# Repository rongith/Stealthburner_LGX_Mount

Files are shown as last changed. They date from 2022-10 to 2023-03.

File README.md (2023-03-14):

# Stealthburner_LGX_Mount

***

1. [Introduction](#introduction)
2. [Credits](#credits)
3. [Parts](#parts)
4. [LGX Mounting](#lgx-mounting)
5. [Features I took care of](#features-i-took-care-of)

***

## Introduction

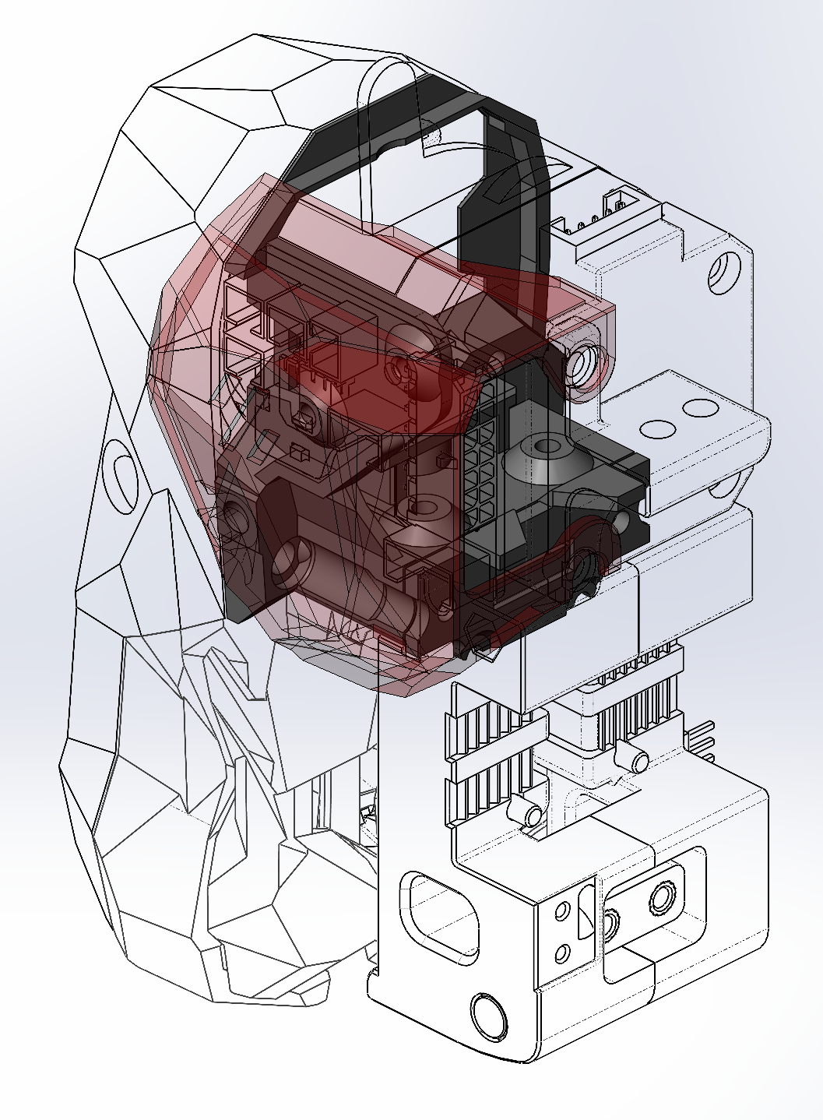
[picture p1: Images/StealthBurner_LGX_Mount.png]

I didn't find a mounting with some bells and whistles I wanted to use my LGX with the Stealthburner. Then I designed my own.

It is be compatible with both versions of rail carriage. The one we screw on the back (Afterburner carriage with CW1) and the one we screw on the front (Stealthburner carriage with CW2).

The Afterburner PCB (LDO) mounting is optionnal. I'm trying to implement the Stealthburner PCB.

The 3D printed parts may not follow the Voron design recommendations.

All photos are not of the same design iteration. I didn't want to shoot the whole sequence of the mounting each time I improved the parts.

## Credits

- Thanx to @errornumber419 for the design of adding the PCB support directly on the mounting.

- The cover is based on wile.e1 cover for Stealthburner and CW1 (<https://github.com/VoronDesign/VoronUsers/tree/master/printer_mods/wile-e1/Stealthburner_CW1_PCB_Cover>)

## Parts

- Mounting options
  - Normal files are in "Standard" folder
  - OctotapV2 files are in "OctotapV2" folder. You can use OctotapV2 files even if you don't have it. It does only level up the mounting to 2mm to set some clearance for the OctotapVé PCB.

| CW1<br>carriage | CW2<br>carriage | All in<br>one part | PCB<br>Support | Files to print|
|:---:|:---:|:---:|:---:|---|
|No|Yes| Yes | No | LGX_SB_Mount-rxxx - 1-2-NoPCB |
|No|Yes| Yes | Yes | LGX_SB_Mount-rxxx - 1-2-PCB |
|Yes|Yes| No | No | LGX_SB_Mount-rxxx - 1-NoPCB / LGX_SB_Mount-rxxx - 2 |
|Yes|Yes| No | Yes | LGX_SB_Mount-rxxx - 1-PCB / LGX_SB_Mount-rxxx - 2|

- Cover

| File to print |
|---|
| [a]_LGX_SB_Cover-rxxx - Standard |

- Additional hardware
  - M3x20 (x2). SHCS / ISO 4762 recommended
  - M3x30 (x2). SHCS / ISO 4762 recommended (M3x25 is enough for the screws on the back mounting)
  - M3x6 (x2). BHCS / ISO7380-1 for the PCB in case you have one.
  - M3 Heat insert (x3).

## LGX Mounting

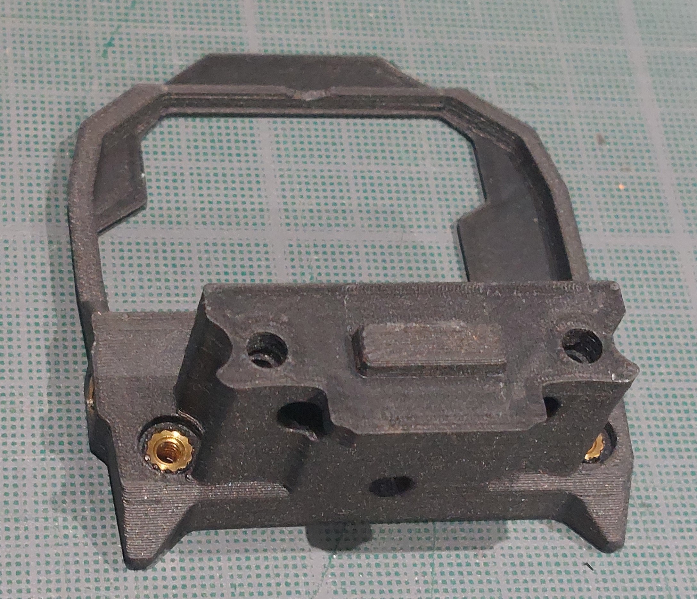
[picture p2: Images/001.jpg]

Put insert in the 3 holes.

Take care to get the insert quite well straight. It is for the Stealthburner to move easily along the M3x25 screws afterward when you want to swap the toolhead.

The insert on the left (of the photo) edge is to screw the cover.

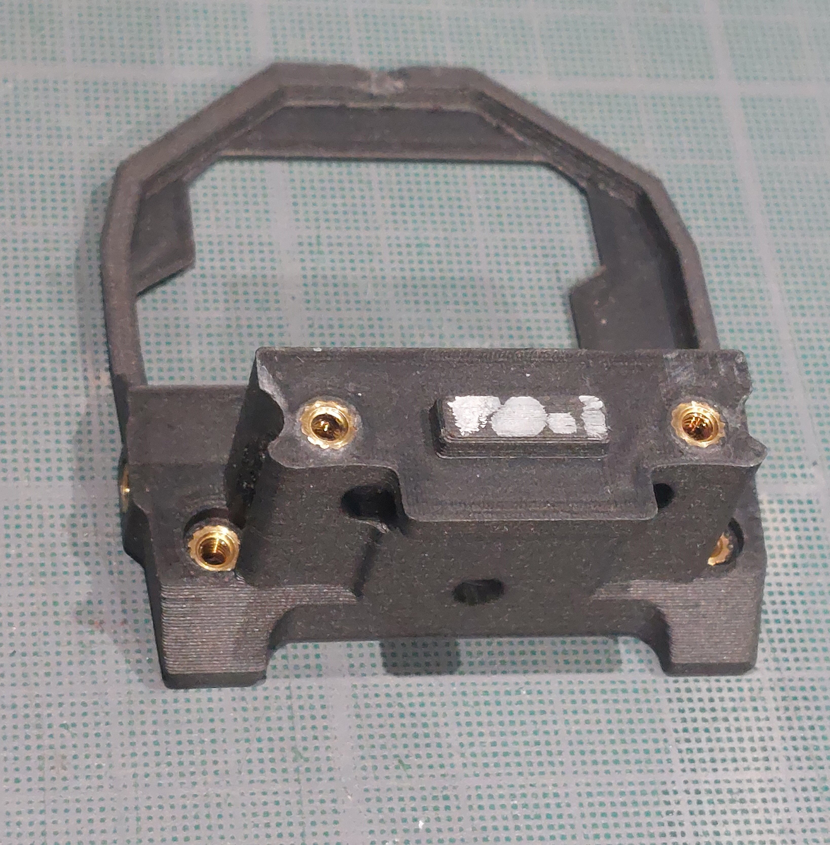
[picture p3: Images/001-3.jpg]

In case you want to use the rail carriage that has holes to screw on the back (CW1), add two more inserts in the back of the part.


    Add the back of the mounting. It should fit on the rectangular joint. Later, it doesn't have to be separated from the mounting. Then I choose to glue it but it is really not mandatory.

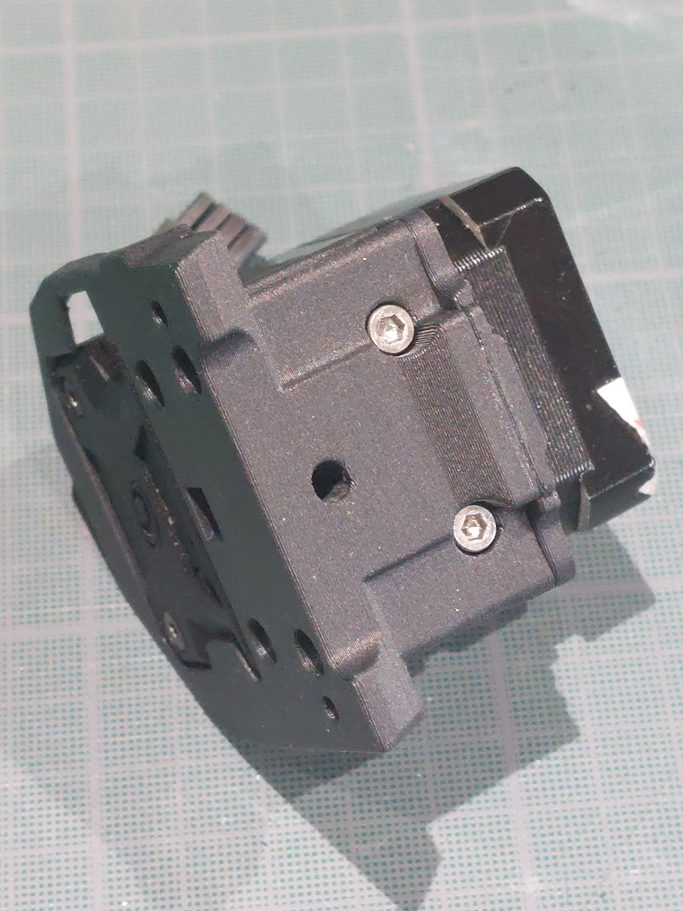
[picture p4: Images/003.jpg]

Screw the bottom with 2 M3x20.

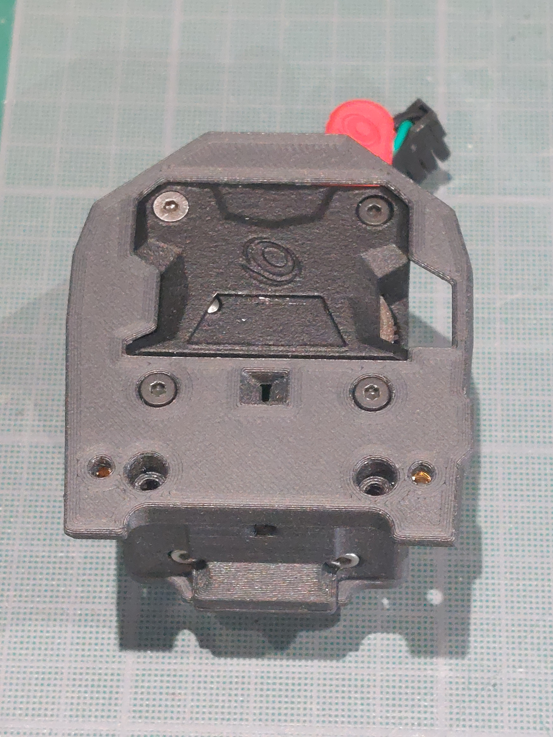
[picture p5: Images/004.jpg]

Screw the front with the provided Bondtech LGX M3x27.

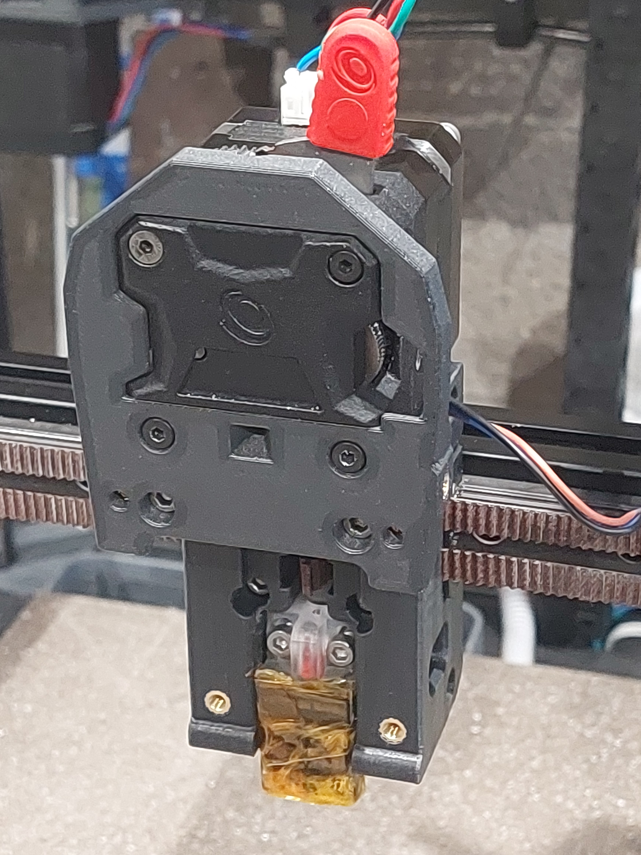
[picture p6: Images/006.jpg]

Screw the mounting on the carriage with 2 M3x30.

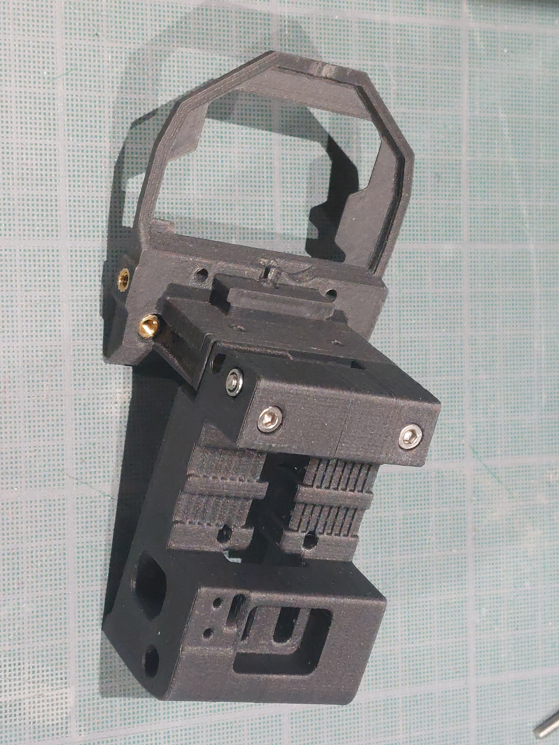
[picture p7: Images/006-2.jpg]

In case you want to use the rail carriage that has holes to screw on the back (CW1), screw the mounting on the carriage with 2x M3x25 or 2x M3X30.

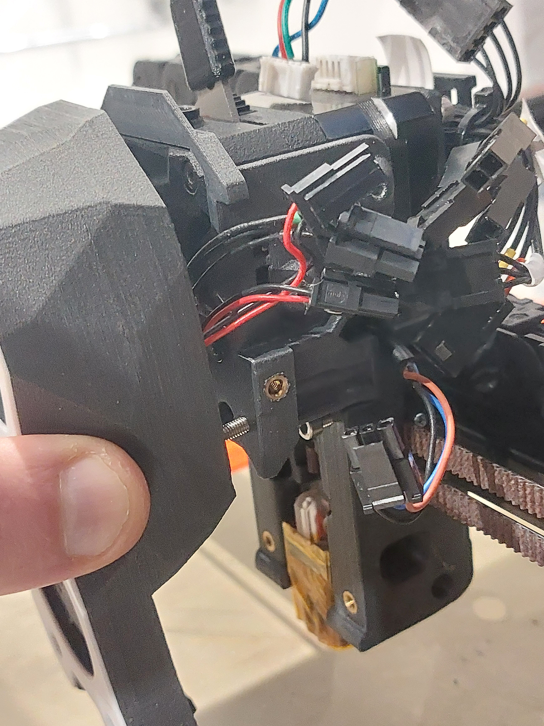
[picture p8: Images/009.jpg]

Screw few turns the Stealthburner M3x25 to hold it.

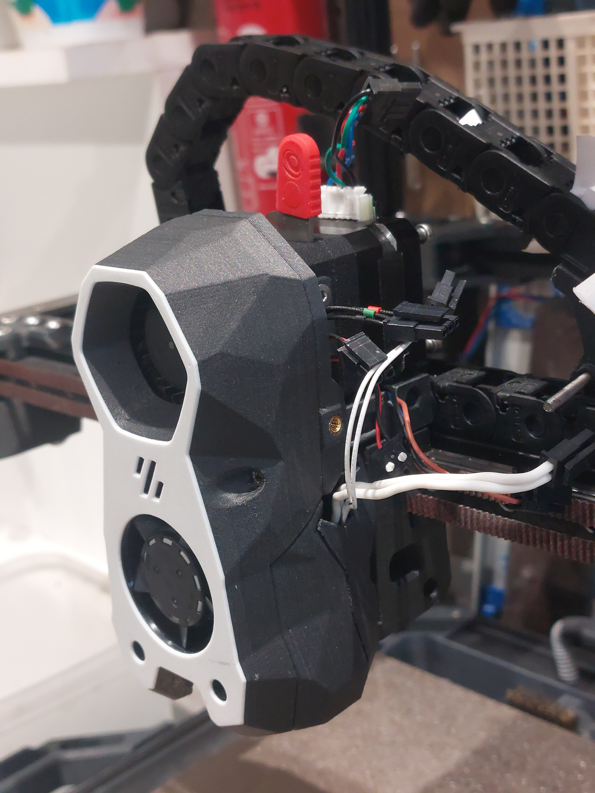
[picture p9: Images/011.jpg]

Mount the toolhead. Take attention to not pinch the toolhead wires between the Stealthburner and its mounting when tighning the whole.

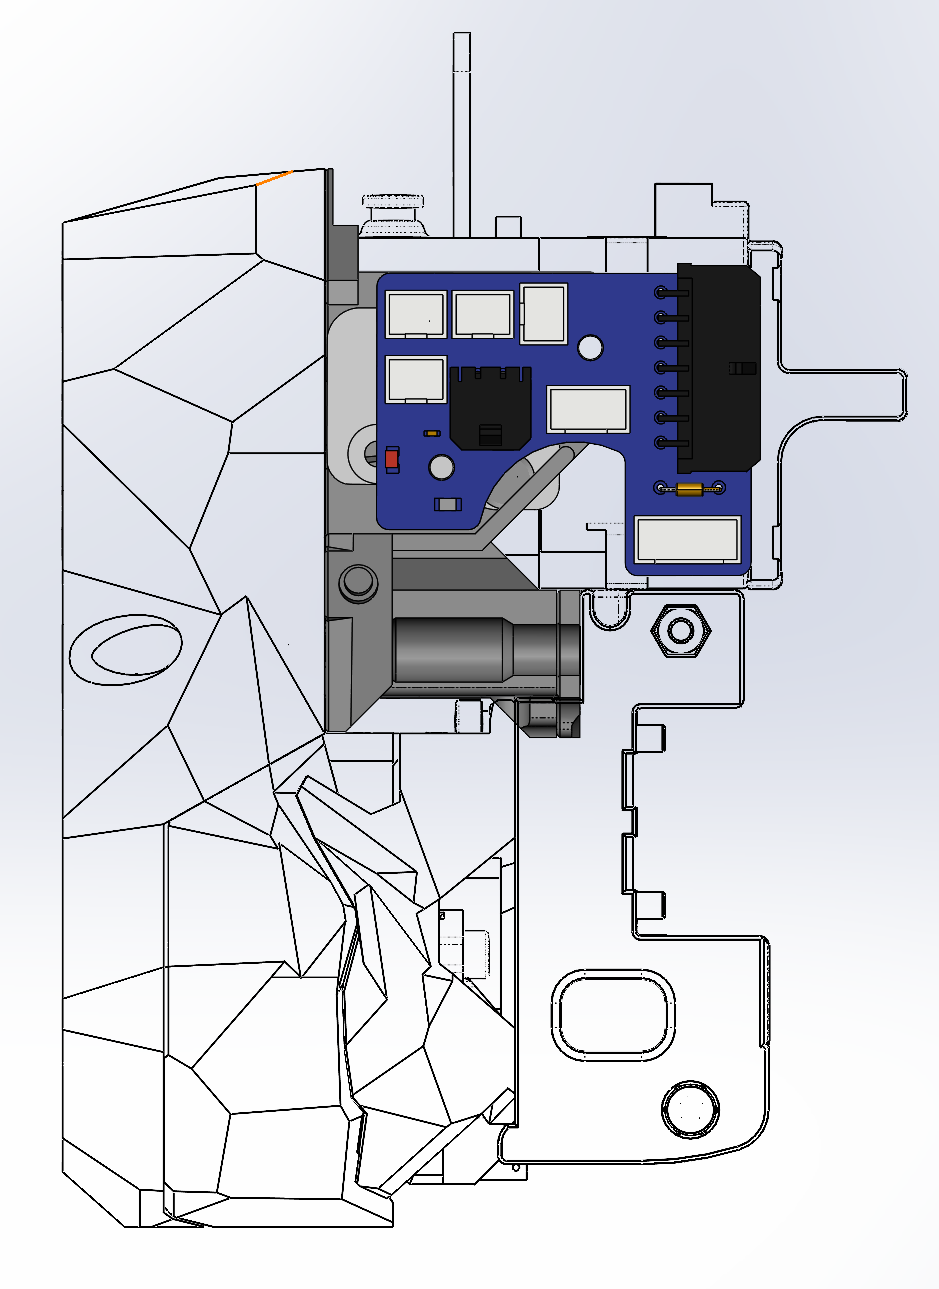
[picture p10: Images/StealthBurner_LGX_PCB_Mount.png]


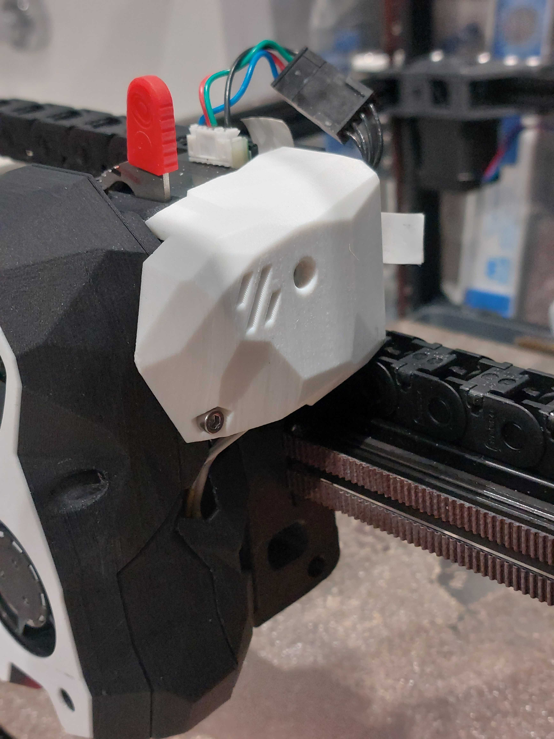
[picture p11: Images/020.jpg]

Screw the cover and Voilà.

## Features I took care of

- Works for CW1 and CW2 rail carriage models.
- Inserts for Stealthburner Fan assembly on the good side.
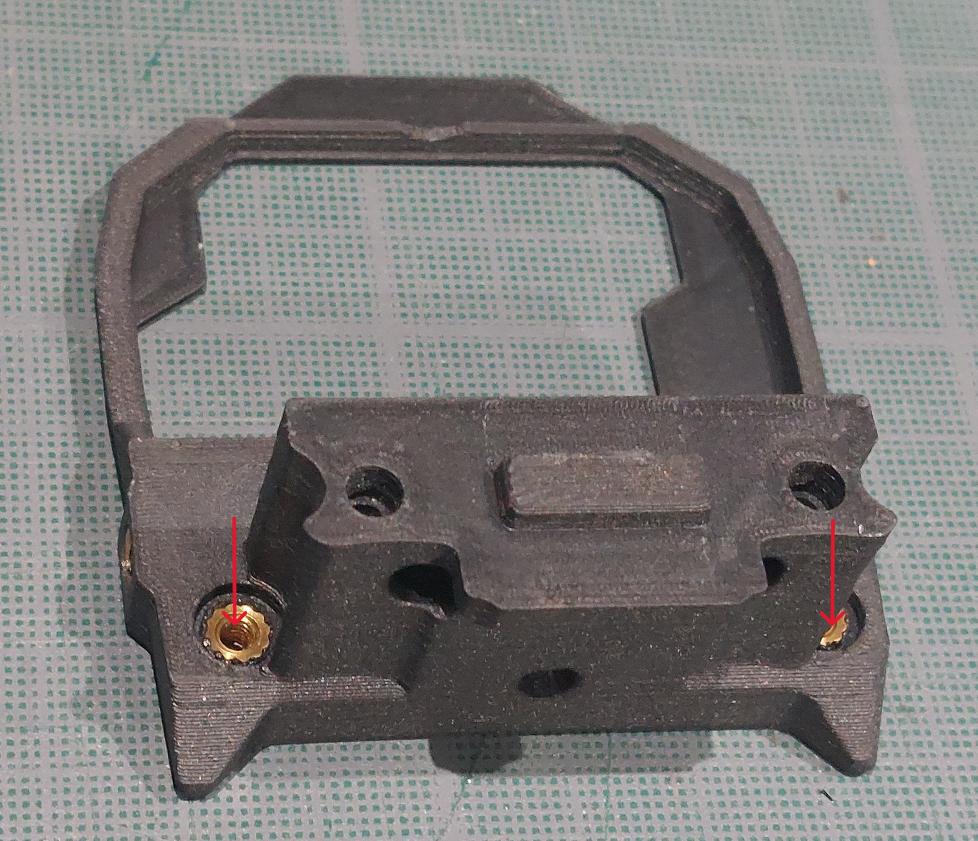
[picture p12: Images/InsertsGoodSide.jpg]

- Can see how far goes your PTFE tube
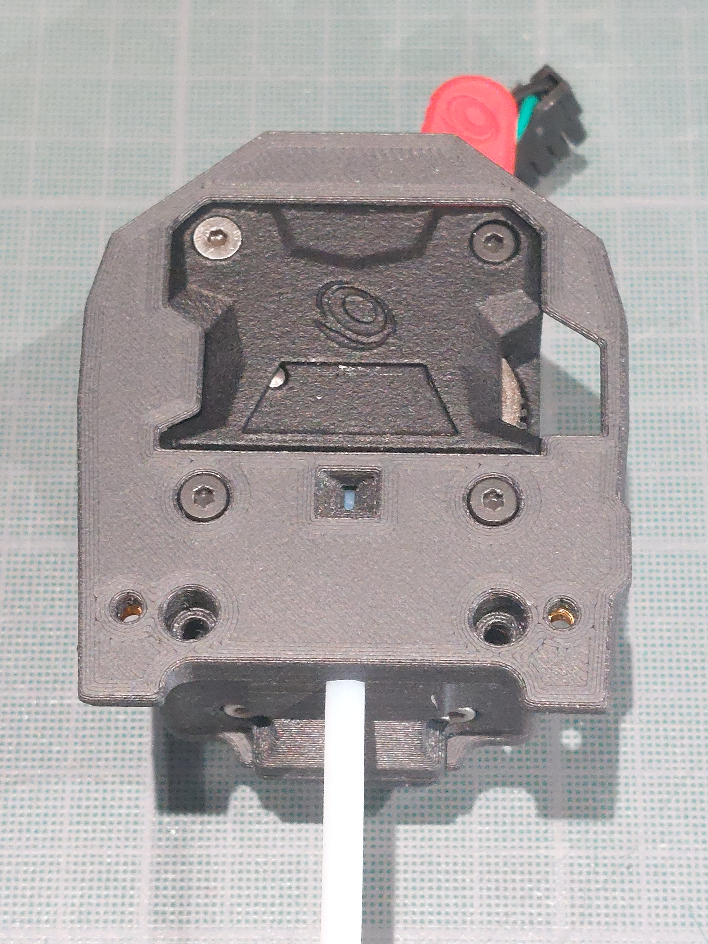
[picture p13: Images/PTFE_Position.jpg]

- Keep some place for your fingers to access the reverse Bowden tube fitting

- Optionnal PCB mounting

- Access to rail top mounting screws

- Access to Toolhead positionning screws
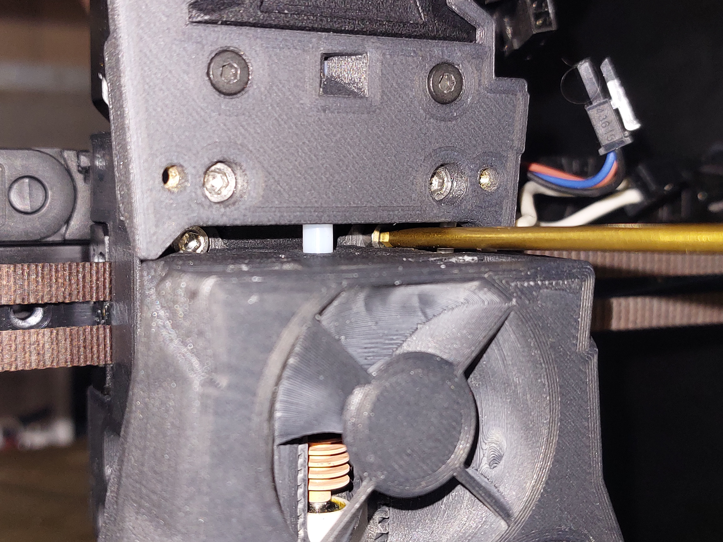
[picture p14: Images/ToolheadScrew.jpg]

- Take care of the clearance between the side cover and the cable chain when X=0

- Printing the mounting in one piece despite some printing in the air. It is still functionnal.
One piece:
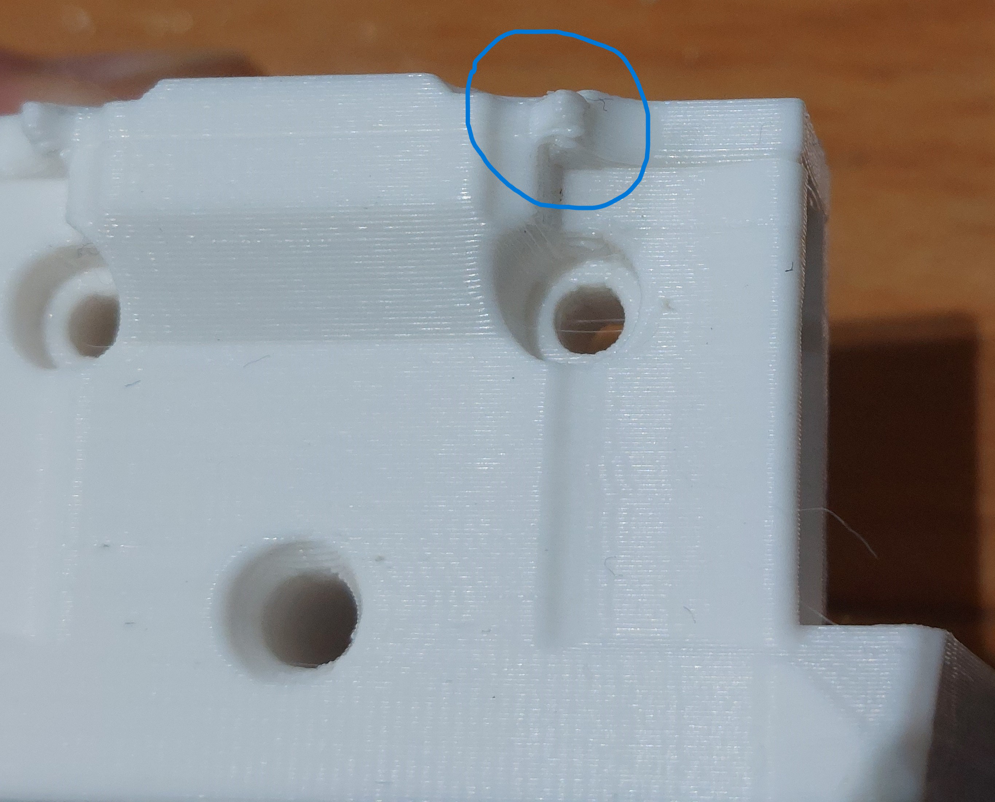
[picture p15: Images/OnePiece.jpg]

Two Pieces (better):
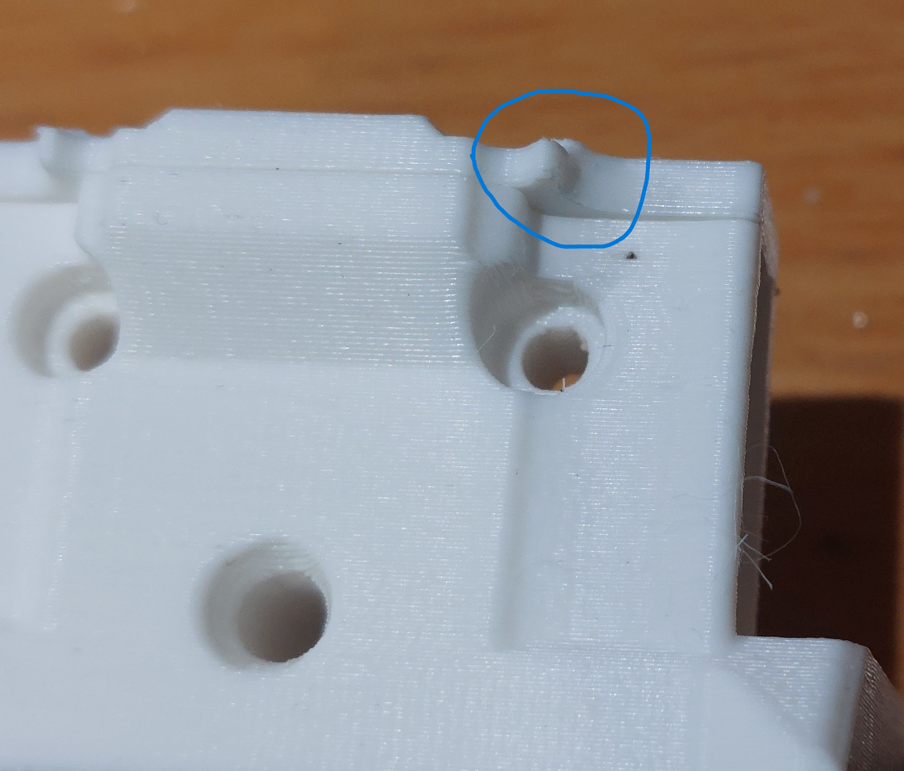
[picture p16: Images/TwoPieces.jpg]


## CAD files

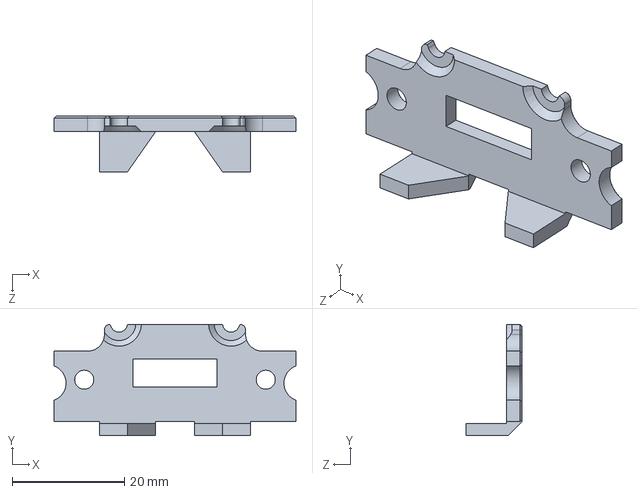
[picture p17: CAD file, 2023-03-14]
CAD/OctotapV2/LGX_SB_Mount-r02i - 2.STEP
43.2 x 19.9 x 10.0 mm

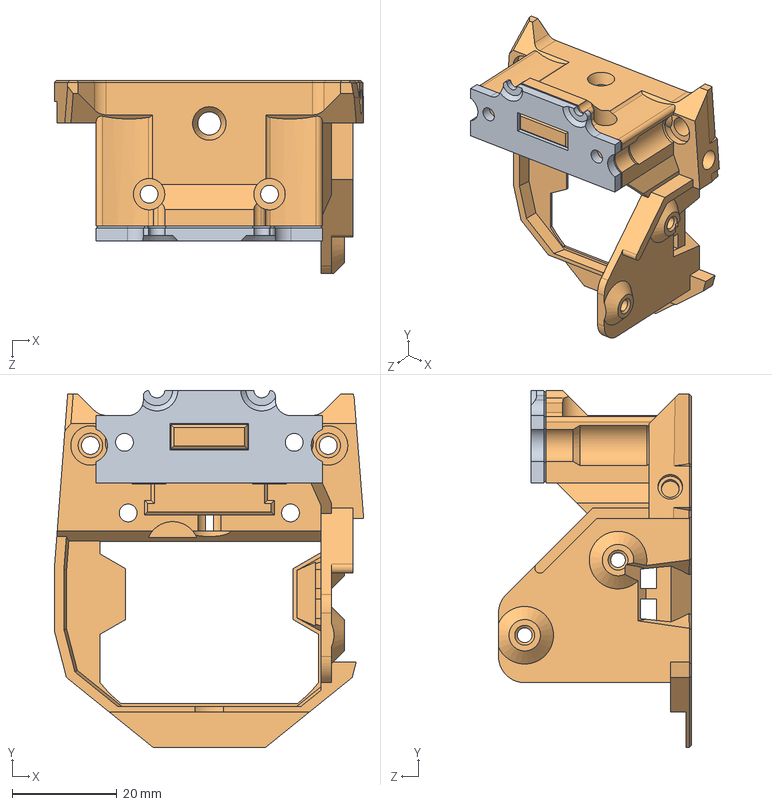
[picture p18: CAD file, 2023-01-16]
CAD/Standard/LGX_SB_Mount-r02e - PCB.STEP
59.1 x 68.2 x 36.8 mm

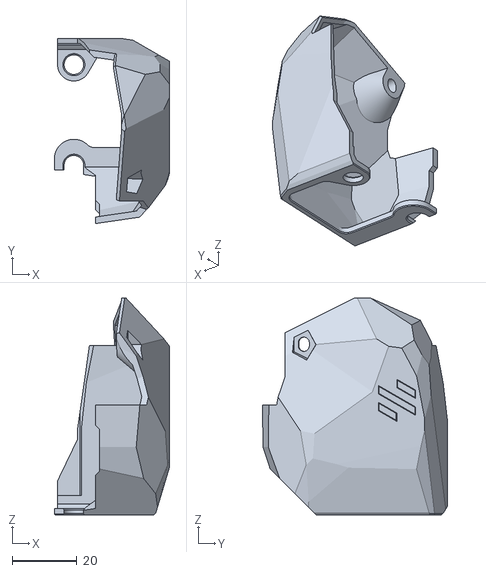
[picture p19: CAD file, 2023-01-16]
STLs/Standard/[a]_LGX_SB_Cover-r00q - Standard.STL
35.5 x 57.1 x 66.9

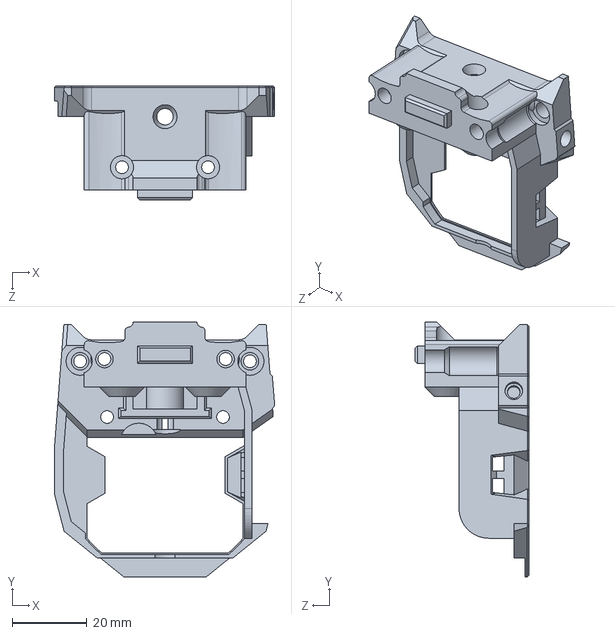
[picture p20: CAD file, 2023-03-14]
CAD/OctotapV2/LGX_SB_Mount-r02i - 1-NoPCB.STEP
58.9 x 68.2 x 30.5 mm

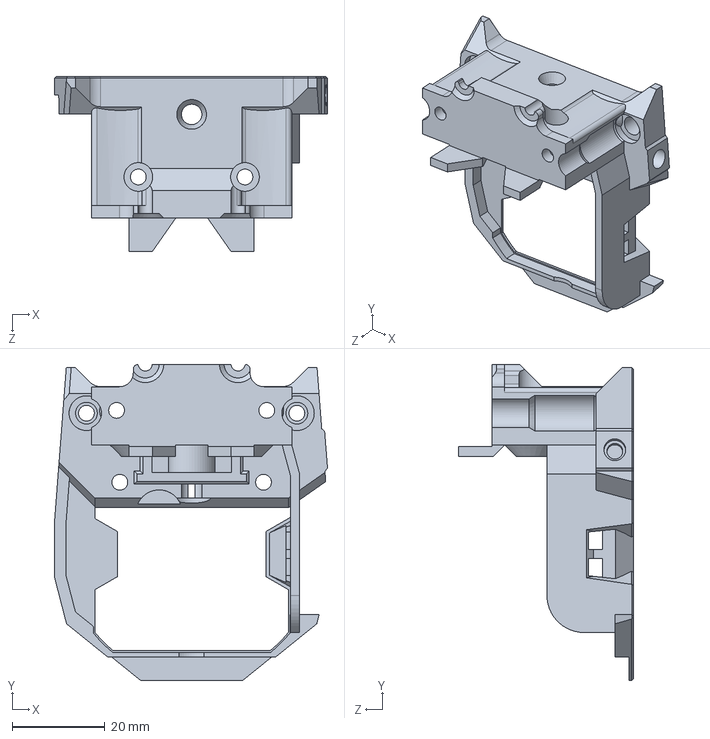
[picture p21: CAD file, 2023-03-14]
CAD/OctotapV2/LGX_SB_Mount-r02i - 1-2-NoPCB.STEP
58.9 x 68.2 x 37.8 mm

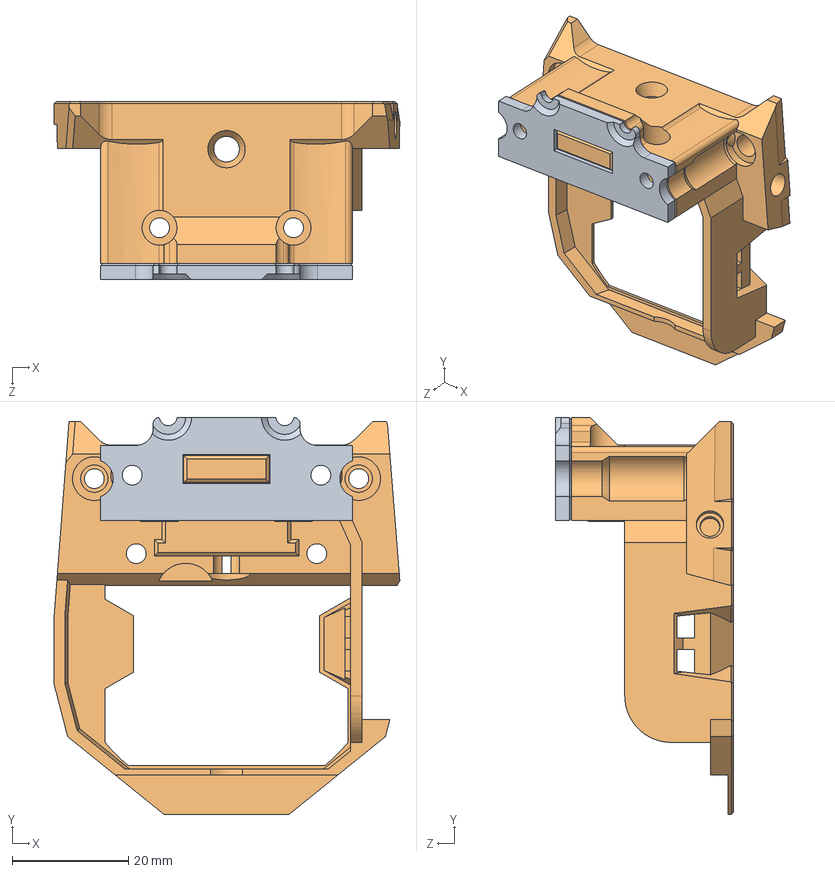
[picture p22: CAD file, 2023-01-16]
CAD/Standard/LGX_SB_Mount-r02e - NoPCB.STEP
59.4 x 68.2 x 30.6 mm

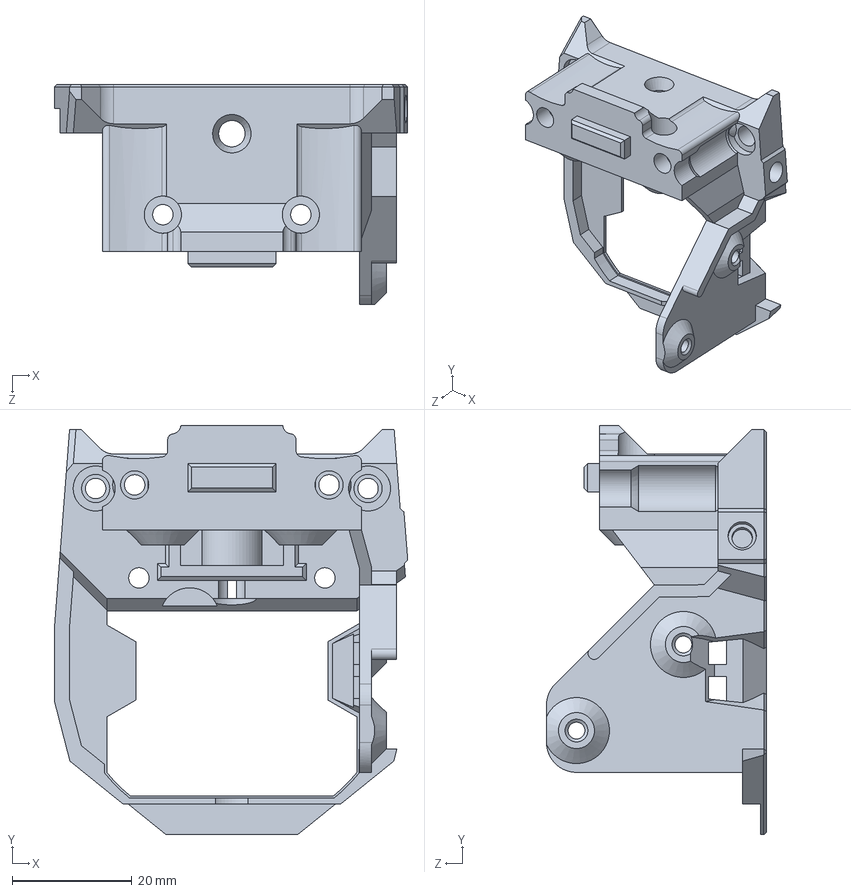
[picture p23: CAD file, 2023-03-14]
CAD/OctotapV2/LGX_SB_Mount-r02i - 1-PCB.STEP
58.9 x 68.2 x 36.7 mm

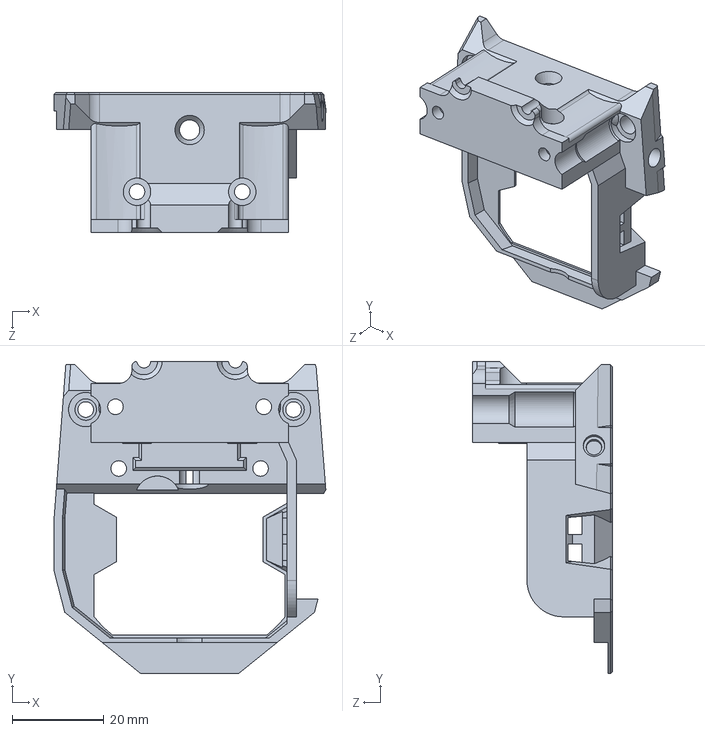
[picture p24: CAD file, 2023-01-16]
CAD/Standard/LGX_SB_Mount-r02e - 1-2-NoPCB.STEP
59.4 x 68.2 x 30.6 mm

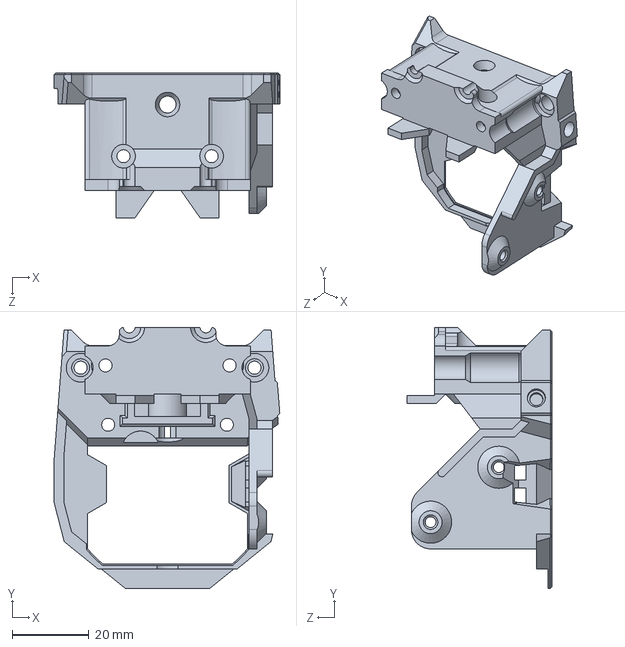
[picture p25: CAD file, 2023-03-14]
CAD/OctotapV2/LGX_SB_Mount-r02i - 1-2-PCB.STEP
58.9 x 68.2 x 37.8 mm

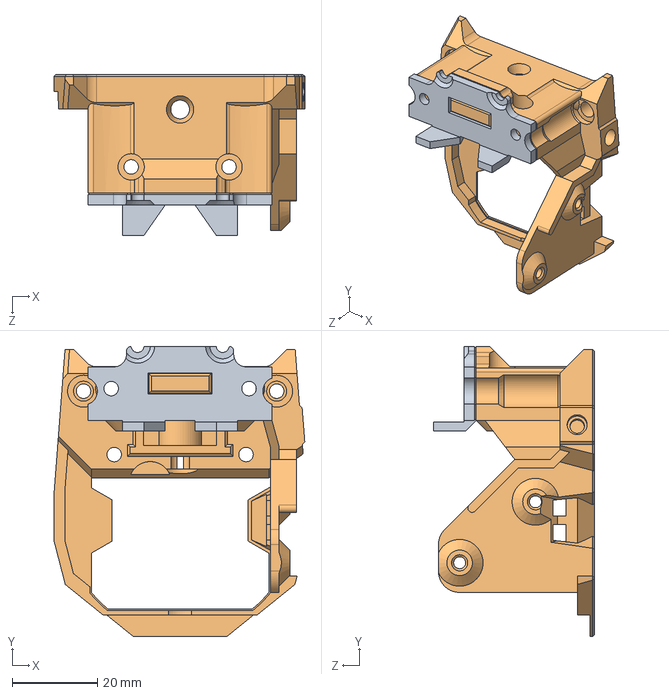
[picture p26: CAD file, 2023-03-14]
CAD/OctotapV2/LGX_SB_Mount-r02i - PCB.STEP
58.9 x 68.2 x 37.8 mm

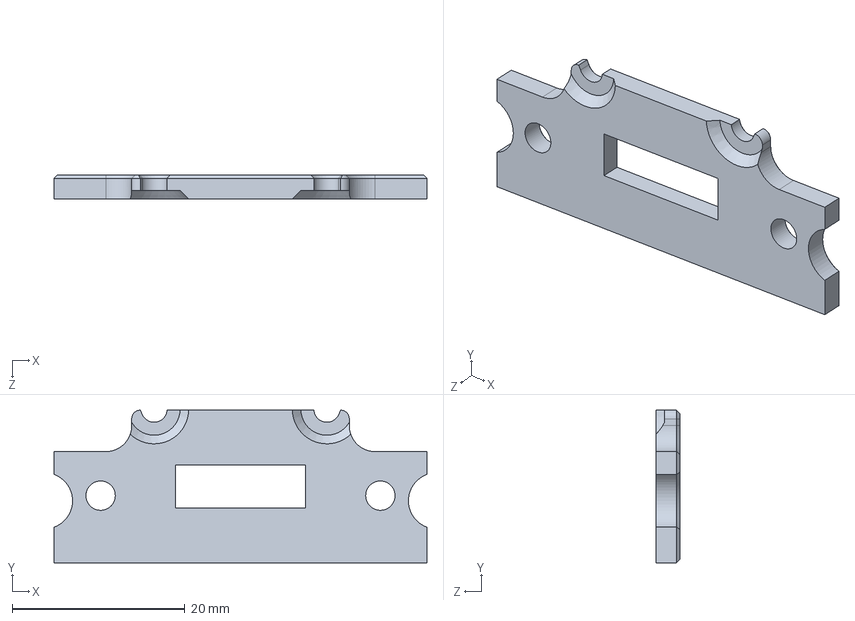
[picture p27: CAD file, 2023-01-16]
CAD/Standard/LGX_SB_Mount-r02e - 2.STEP
43.2 x 17.7 x 2.80 mm

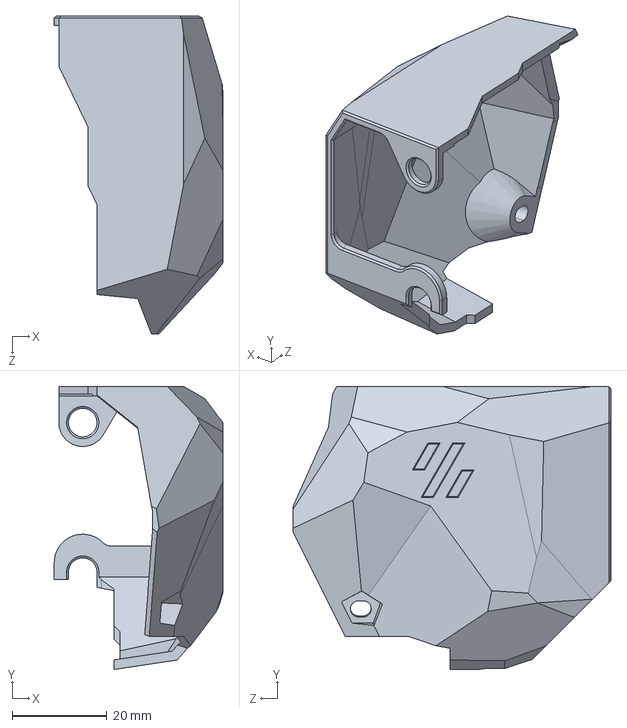
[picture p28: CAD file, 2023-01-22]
CAD/OctotapV2/LGX_SB_Cover-r00r - Standard.STEP
35.5 x 59.6 x 66.9 mm

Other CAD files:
CAD/Standard/LGX_SB_Cover-r00q - Standard.STEP
CAD/Standard/LGX_SB_Mount-r02e - 1-NoPCB.STEP
CAD/OctotapV2/LGX_SB_Mount-r02i - NoPCB.STEP
CAD/Standard/LGX_SB_Mount-r02e - 1-2-PCB.STEP
CAD/Standard/LGX_SB_Mount-r02e - 1-PCB.STEP
STLs/OctotapV2/LGX_SB_Cover-r00r - Standard.STL
STLs/OctotapV2/LGX_SB_Mount-r02i - 1-2-NoPCB.STL
STLs/OctotapV2/LGX_SB_Mount-r02i - 1-2-PCB.STL
STLs/OctotapV2/LGX_SB_Mount-r02i - 1-NoPCB.STL
STLs/OctotapV2/LGX_SB_Mount-r02i - 1-PCB.STL
STLs/OctotapV2/LGX_SB_Mount-r02i - 2.STL
STLs/Standard/LGX_SB_Mount-r02e - 1-2-NoPCB.STL
STLs/Standard/LGX_SB_Mount-r02e - 1-2-PCB.STL
STLs/Standard/LGX_SB_Mount-r02e - 1-NoPCB.STL
STLs/Standard/LGX_SB_Mount-r02e - 1-PCB.STL
STLs/Standard/LGX_SB_Mount-r02e - 2.STL

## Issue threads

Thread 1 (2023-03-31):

EBB SB2209/2240 version

sprior, 2023-03-31:
I've got an LGX and just got an EBB SB2240 toolhead board and it looks like some changes would be needed to use your design.  I'm still investigating what might need to change but thought I'd mention it in case others would need the same.

rongith, 2023-03-31:
Due to the optimized design of those parts for the CW2, there is no room to fit it along an LGX.
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
The LGX is too wide compared to the CW2.
You would need to expend the SB fan body part too to mount the PCB on the right side properly.

sprior, 2023-03-31:
Ok thanks, I didn't find any info on this before I bought the board so I guess I'll return it.  This issue can serve as some documentation that it won't work without other significant changes.

rongith, 2023-03-31:
I just imported the BTT models in my CAD after you asked. I add suspicions because I already imported the 2 parts PCB for afterburner. It is a confirmation. I had very few informal requests about that before but I delayed the check. As you, I just wanted it because in the meantime I will switch to CAN wiring. We will have to find an other solution then.

rongith, 2024-09-03:
I'm working on that.
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

Closed 2023-03-31.

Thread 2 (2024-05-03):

Add support for Filametrix + toolhead and entry sensors

BenBergman, 2024-05-03:
This is probably a tall ask since the extruder body isn't a printed part, but it is what I've got and I want to use it with Filametrix.

I'll try modelling this when I have time, but thought I'd start the issue at least in case I don't get to it before someone else does.

rongith, 2024-05-03:
You would need to provide some CAD files from a Filametrix. Then I may see how difficult your request is.

Closed 2024-07-10.

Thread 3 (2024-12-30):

STL for cable chain adapter?

ELK169, 2024-12-30:
Hi! I appreciate your work very much. I just can't find the STL file for the adapter between the the back side of the stepper motor and the cable chain. Is this part your own creation or can I find it elsewhere?
MfG ELK

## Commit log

2022-10-26 First publication
    [LGX-GearCover-r00b.STEP, LGX-GearCover-r00b.STL, LGX-Mount-SW-r00l-1.STL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]
2022-10-26 Afterburner carriage
2022-11-01 Fix counterbore printability removed accidentally
    [LGX-Mount-SW-r00l-1.STL, LGX-Mount-SW-r00l-2.STL, LGX-Mount-SW-r00l.STEP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]
2022-11-21 Cover added. Small adjustments.
    Cover based on wile.e1 design added.
    [LGX-Mount-SW-r00n-1.STL, LGX-Mount-SW-r00n-2.STL, LGX-Mount-SW-r00n.STEP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]
2022-11-21 Part orientation and accent naming
    [LGX_Stealthburner_Cover-r00g - PCB-2.STEP, LGX_Stealthburner_Cover-r00g - PCB-2.STL, [a]_LGX_Stealthburner_Cover-r00g - PCB-1.STL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]
2022-12-09 Cover compatibility for Voron-Tap
    [LGX_Stealthburner_Cover-r00g - PCB-1.STEP, LGX_Stealthburner_Cover-r00g - noPCB.STEP, LGX_Stealthburner_Cover-r00h - PCB-1.STEP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]
2023-01-16 PCB support
    PCB support (optionnal)
    Side refactoring
    Bigger cover
    Better clearance for cover
    [LGX-GearCover-r00b.STEP, LGX-GearCover-r00b.STL, LGX-Mount-SW-r01d - 1.STEP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]
2023-01-22 Beta Octotapv2 compatible
    [LGX_SB_Cover-r00r - Standard.STL, LGX_SB_Mount-r02f - 1-2-NoPCB.STEP, LGX_SB_Mount-r02f - 1-2-NoPCB.STL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]
2023-01-22 Add cover STEP
    [LGX_SB_Cover-r00r - Standard.STEP]
2023-01-23 Readme PCB clarification
2023-03-14 OctotapV2 released out of beta
    [LGX_SB_Cover-r00q - Standard.STEP, LGX_SB_Cover-r00r - Standard.STEP, LGX_SB_Cover-r00r - Standard.STL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]
